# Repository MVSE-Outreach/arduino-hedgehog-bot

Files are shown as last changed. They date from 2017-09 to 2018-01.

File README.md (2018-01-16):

# [Hedgehog Bot](http://hedgehogbot.digimakers.co.uk)

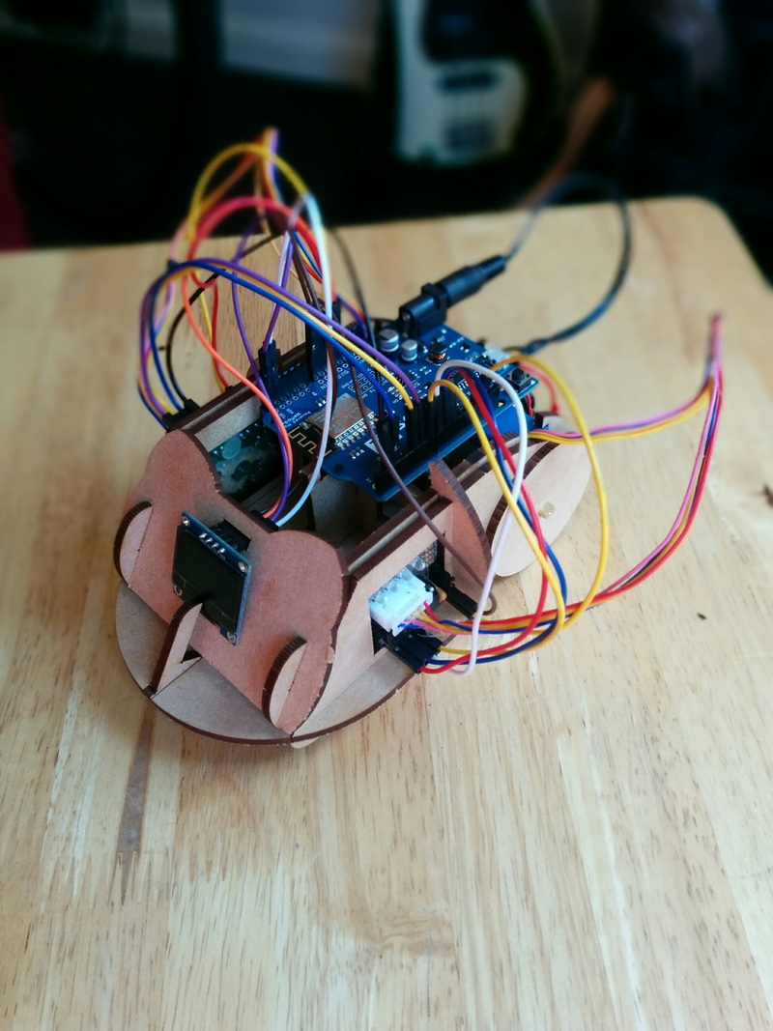
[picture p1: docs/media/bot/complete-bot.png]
Hedgehog bot (http://hedgehogbot.digimakers.co.uk)


The Hedgehog bot is a robotic platform powered by the
[ESP8266](http://espressif.com/en/products/hardware/esp8266ex/overview)-based
[Wemos D1 R2](https://wiki.wemos.cc/products:d1:d1) development board.

Notable Features:
* Full laser cut MDF construction
* Dual servo motor drive
* 128x64 OLED display
* WiFi (client and access point modes)

Instructional videos are available on [YouTube](https://www.youtube.com/playlist?list=PLFSZW1PcP6gNI3f4X1cLMgz0ljdSJu5kU)

If you're interested in learning more, visit the hedgehog bot website:
http://hedgehogbot.digimakers.co.uk 

If you're a volunteer or workshop lead who wants to learn more, check out the
[facilitator notes](#facilitator-notes)

----

## Software setup

### Prerequisites

* [CH340 Drivers](http://www.nerdkits.com/usb-serial/ch341.php)

### Installation
#### Windows or Mac OS X
1. Copy `hhb_blink`, `hhb_bot`, and `hhb_wifi` from `sketches` into your Arduino sketchbook folder
2. Copy the folders in `libraries` to the `libraries` folder in your Arduino
   sketchbook folder, if it doesn't already exist you can just copy and paste
   the `libraries` folder straight into the sketchbook folder.
3. Verify that when you run the Arduino IDE and click the menu options `File -> Sketchbook`
   you can now see:
   - `hhb_blink`
   - `hhb_bot`
   - `hhb_wifi`

#### Linux (Raspberry Pi)

```sh
$ git clone --recursive https://github.com/MVSE-Outreach/arduino-hedgehog-bot.git hedgehog-bot
$ cd hedgehog-bot
$ ./install.sh <PATH-TO-ARDUINO-SKETCHBOOK>
```

----

## Facilitator notes

Most things are documents within the `docs` folder in the repository including:

* Instructions on ordering parts: [docs/kit-ordering.md](docs/kit-ordering.md)
* Troubleshooting: [docs/troubleshooting.md](docs/troubleshooting.md)
* Preparing a workshop: [docs/preparing-a-workshop.md](docs/preparing-a-workshop.md)
* Components used in the Hedgehog bot: [docs/components.md](docs/components.md)

### Laptop setup

* Download the laptop setup script.
* Copy the script over to a memory stick.
* Run the script to set up a computer **at least once** to download the
  necessary dependencies.
* Copy the script along with the files and folders adjacent to the script that
  it downloaded in the previous step to other memory sticks used to set up
  laptops.
* Run the script from the memory stick on all other laptops that need setting
  up, after the first run the dependencies will be downloaded so subsequent
  setups should be much faster.

----

## Known issues
- Arduino Nano not recognised: Have you installed CH340 drivers?
- WiFi not working: Test 9V battery

See the [troubleshooting docs](/docs/troubleshooting.md) for more

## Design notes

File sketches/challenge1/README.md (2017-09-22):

# arduino-sketch-hedgehog-bot-blink

An Arduino Sketch for the HedgeHog bot that blinks the LED on and off.

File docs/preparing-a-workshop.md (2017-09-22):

# Preparing a workshop

## Ordering parts

### Suppliers

[Aliexpress](https://www.aliexpress.com/) has the best prices for the parts we
use, however it has lead times of ~40 days so is best suited to bulk orders
for 100s of kits.

[Banggood](https://www.banggood.com/) has traditionally been the source of
parts for the kits with slightly better shipping times than Aliexpress,
typically 7-20 business days.

[eBay](http://ebay.co.uk/) and [Amazon](amazon.co.uk) have been used for parts
when we've been up against short deadlines needing to prep for workshops with
a few weeks notice. It tends to cost a lot per bot, hence whenever we can we
try and buy from China.

Banggood is considerably more expensive than Aliexpress (Will Price conducted
a comparison in Sept 2017 for pricing for 100 bots, Aliexpress came out at
~£10/bot, and Banggood at ~£18/bot).

Both [buyabattery.co.uk](https://www.buyabattery.co.uk/procell-9v-batteries-box-of-50-bulk-now-duracell-industrial.html),

[batterystation.co.uk](https://www.batterystation.co.uk/9v-batteries/industrial-by-duracell-9v-pp3-6lr1-id1604-batteries-box-of-50),
and [LYCO](https://www.lyco.co.uk/duracell-industrial-alkaline-batteries-9v-pack-of-50.html)
provide good prices for 9V batteries in boxes of 50 pieces. They Have next day delivery for not much money.

### Choosing a supplier

Factors of consideration:

* How long have you got until the workshop?
* How many kits do you need?
* How many kits are in currently in inventory?
* How long until you need the parts in working days? Remember it takes a full
  day to put together a set of kits and you'll need to organise people to help
  you do this. It takes a while for the order to filter through university
  purchasing and actually be placed, again you have to account for this.

| Supplier | Typical lead time (working days) | Comments |
|---|---|---|
| [Aliexpress](https://www.aliexpress.com/) | 40 | We haven't had experience placing an order from Aliexpress yet |
| [Banggood](https://www.banggood.com/) | 7-20 | Typically arrive in under a month from placing an order |

## Putting together kits

* Choose an afternoon and advertise for helpers on the SCEEM facebook group (3 or
  4 is a good number)
* Get envelopes to store each kit in
* Set up a packing line to produce kits
  * Each person is responsible for placing a small number of components into
    the envelope they are passed. They should have the parts close to them to
    minimize the time it takes to put parts into the kits.
  * Check the first kit produced by the packing line against the kit listing
    to ensure no parts have been missed

## Setting up university laptops

NOTE: You'll need admin access to set up a university laptop.

Follow the [installation instrutions](laptop-setup.md).

## Sampling and verifying kits (with university laptops)

* Randomly sample 10% of the kits you have prepared
* Check all parts are present
* Build the kits following the instructions on [hedgehogbot.co.uk](http://hedgehogbot.co.uk)
* Program each of the bots with
  [challenge2](http://www.hedgehogbot.co.uk/challenge2.html) ensuring that the bots can move and the screen displays a face

## Final checks

* [ ] Ensure all the laptops that are going to the workshop have been set up.
* [ ] Ensure you have enough kits for the workshop (ideally bring 10% extra).
* [ ] Plan for component failure and bring spares of each component.
* [ ] Bring files in case the bodies are incorrectly produced and need fettling.

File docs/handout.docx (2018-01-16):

# Hedgehog bot

# Parts checkt

Check that you have the following parts in your pack.

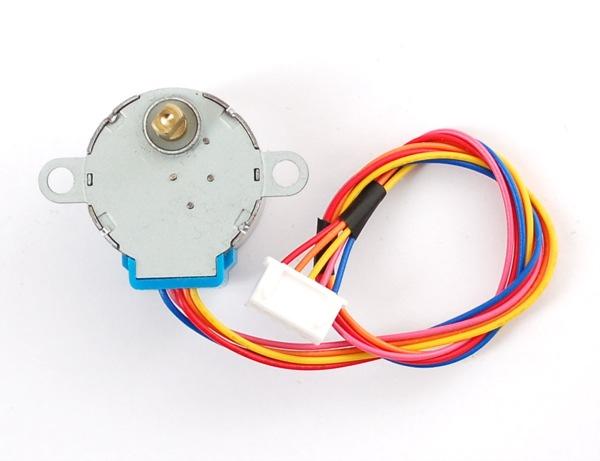
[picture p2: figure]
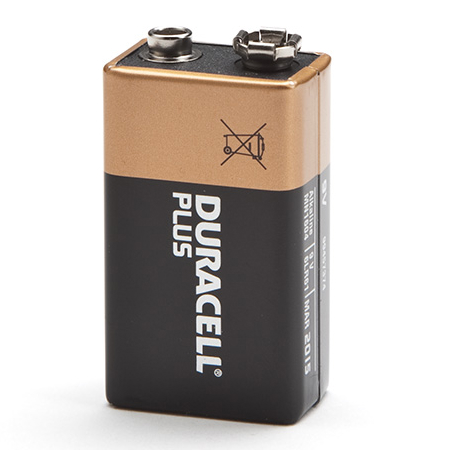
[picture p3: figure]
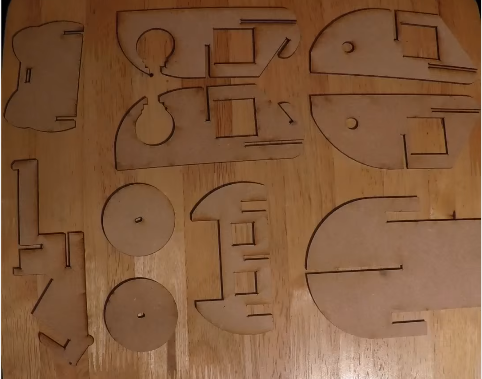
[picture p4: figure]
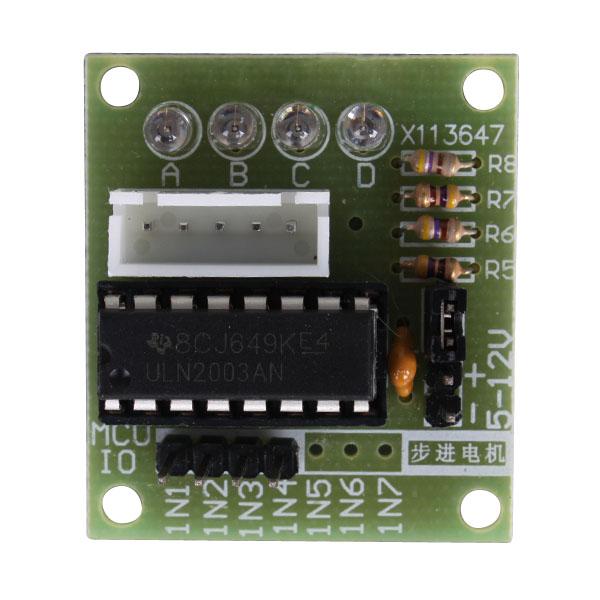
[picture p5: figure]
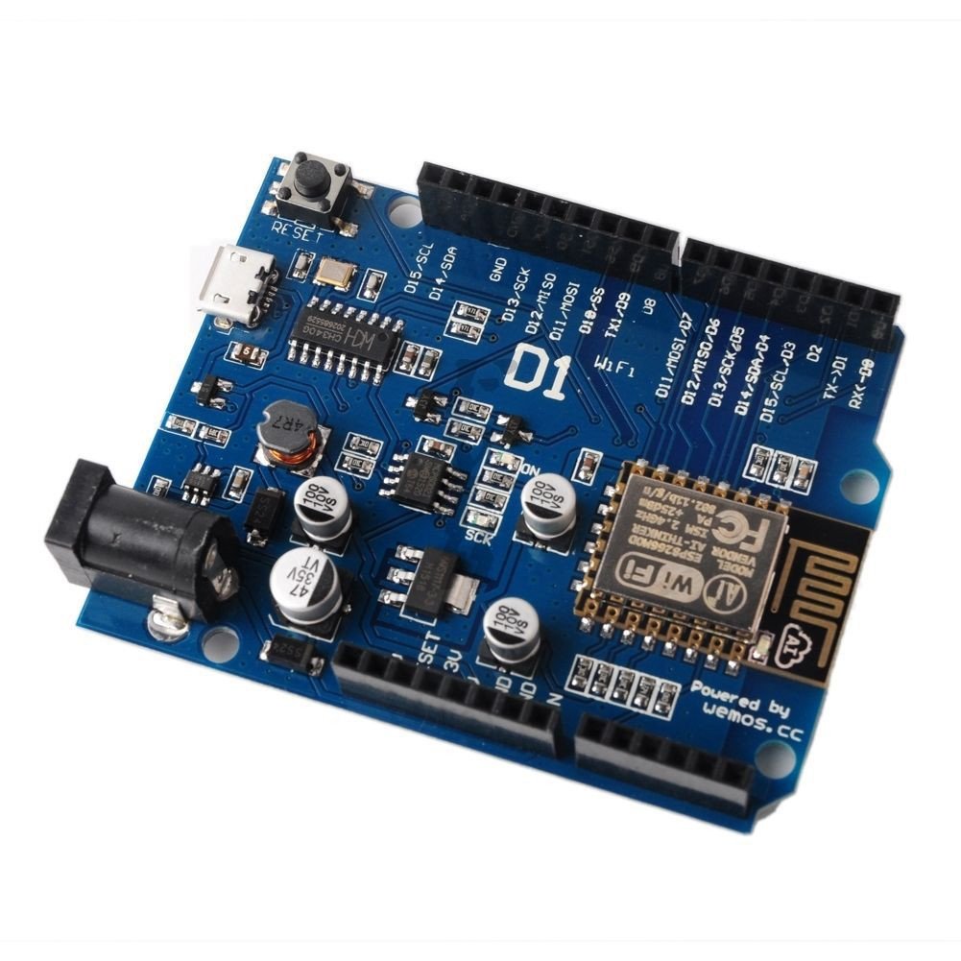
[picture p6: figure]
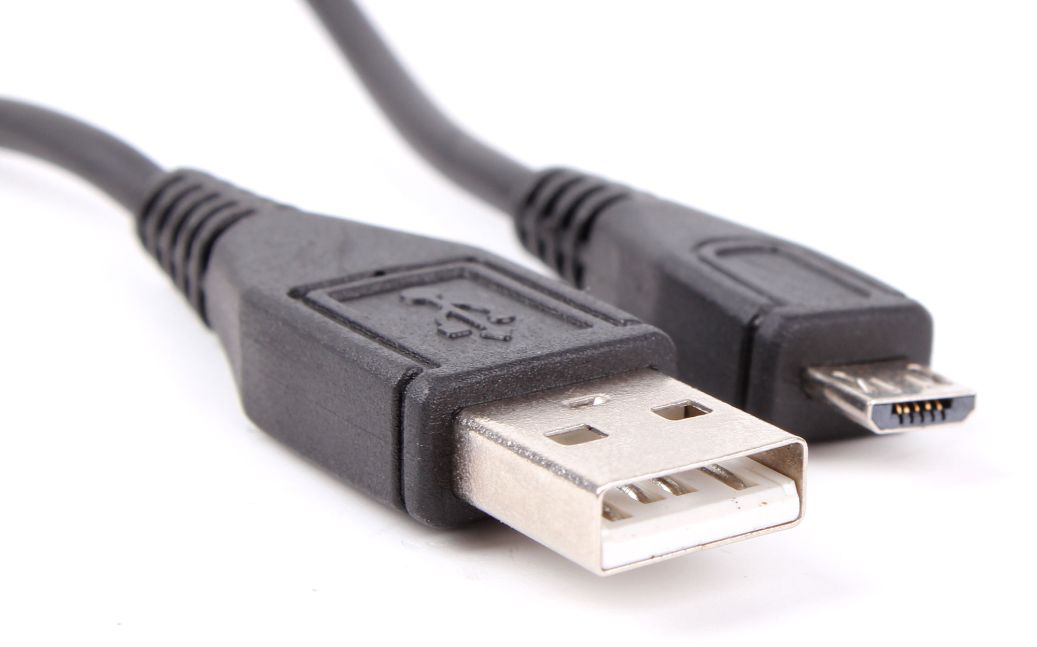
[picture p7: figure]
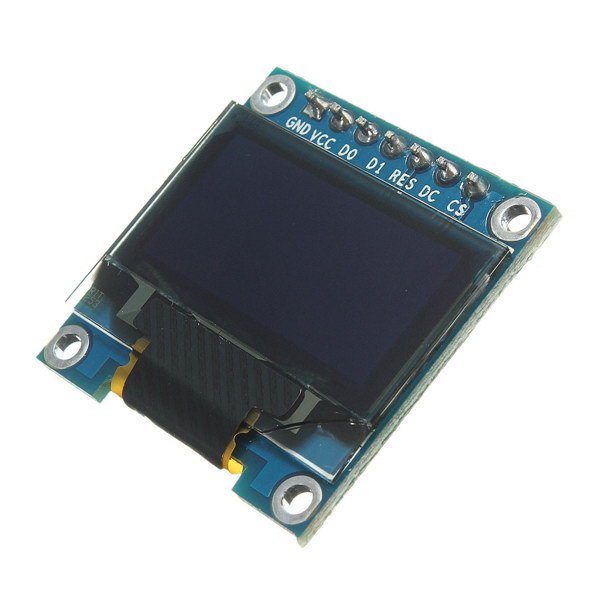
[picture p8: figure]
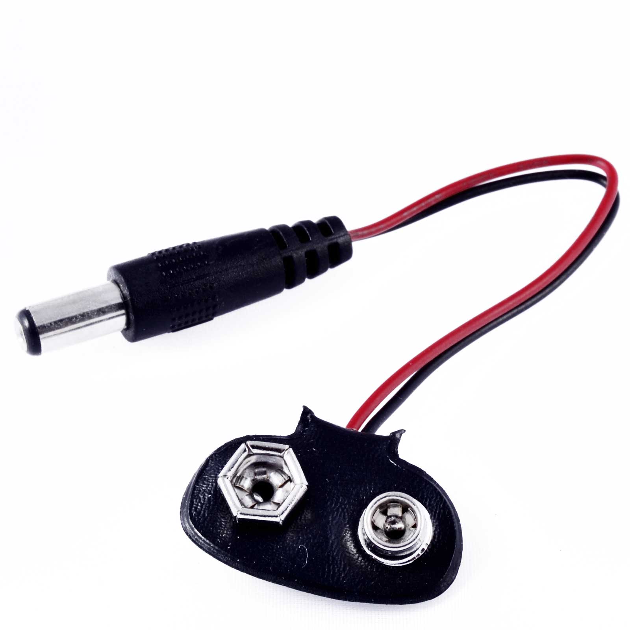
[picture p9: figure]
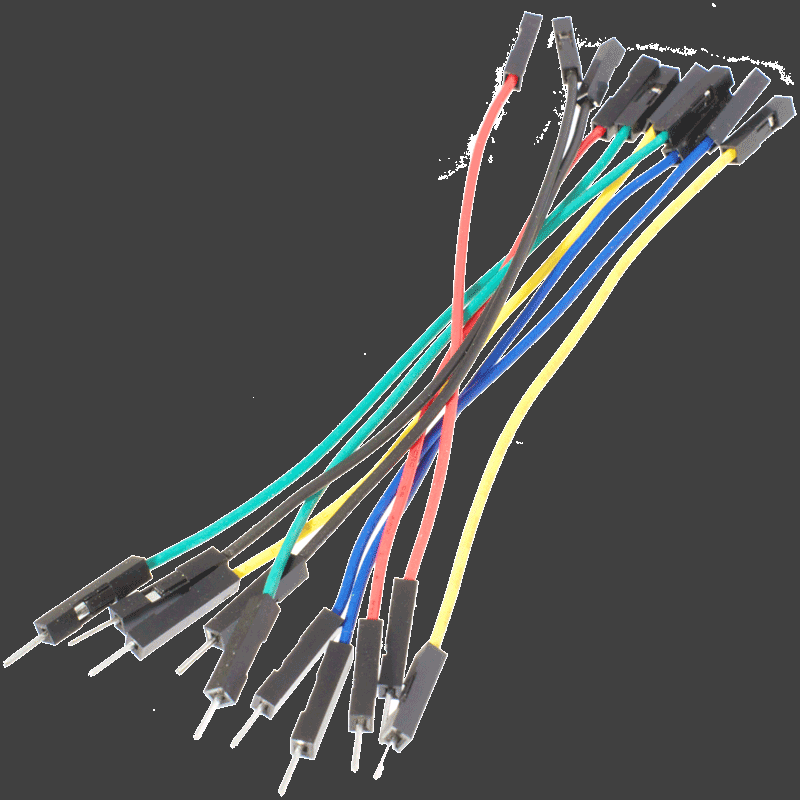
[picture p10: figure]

# Computer setup

Open http://www.hedgehogbot.co.uk/setup.html to setup your computer with the Arduino IDE, esp8266 board package for Arduino, and the hedgehog bot libraries.

In short:

- Grab a memory stick
- Copy and paste the Arduino setup file and extract/run it
- Open Arduino, select File > Preferences and type http://arduino.esp8266.com/stable/package_esp8266com_index.json into Additional Boards Manager URLs
- Close the Preferences window
- Select Tools > Boards > Board Manager and click on esp8266 and press the Install button
- Close the Board manager window
- Copy the contents of the folder Arduino > All > libraries to Documents > Arduino > Libraries

# Get building!

Open http://www.hedgehogbot.co.uk/ and select “Challenge 1: LED”, or if you’re still waiting to setup your computer, skip ahead and start building your robot by looking at “Challenge 2: Bot”, you can go back to Challenge 1 once your bot is built.

Progress through challenges 1-3.

We’re here to help, if you get stuck, please come and ask one of us for help. If you’ve completed all the challenges and want to go further, come and have a chat too!

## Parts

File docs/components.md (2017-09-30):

# MDF body

* 3mm MDF
* If producing cuts for other pieces to fit into, take account of total width of pieces 
  and add ~0.3mm extra for a bit of room otherwise the bits are very hard to put together

# ULN2003 driver boards

* ULN2003 driver
* 32x35x1.5mm
* 4 pin input: IN{1..4}
* 4 pin power input: Vdd, Vcc, jumper to determine whether board is on or off (jumpered = on)

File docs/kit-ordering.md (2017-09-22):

# Ordering in bulk to produce a kit

## Part list

| Part image | Part | Quantity per bot | Comments |
|---|---|---|---|
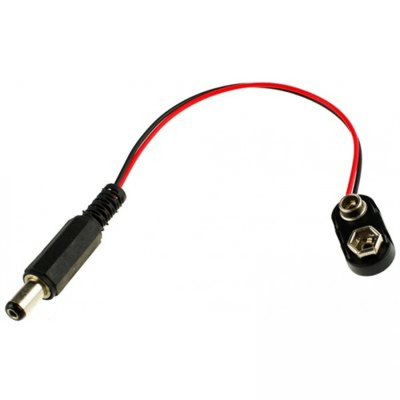
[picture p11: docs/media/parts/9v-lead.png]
9V lead
|  | 9V Lead with barrel jack | 1 | Make sure you get leads with a barrel jack |
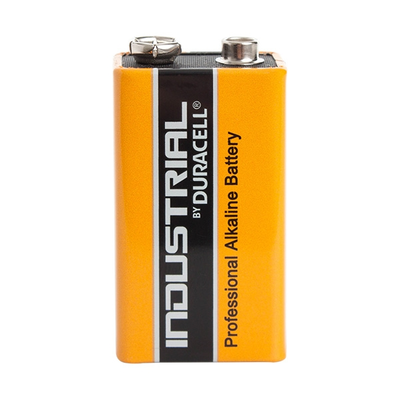
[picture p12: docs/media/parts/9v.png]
9V battery
|  | 9V battery | 1 | Sometimes kids go through more than a single battery in a single session |
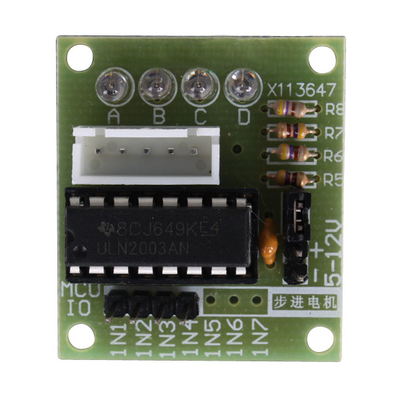
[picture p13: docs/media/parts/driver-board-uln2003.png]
Motor drive board
|  | ULN2003 Stepper motor driver board | 2 | Needs to be this exact board as the body is designed for it |
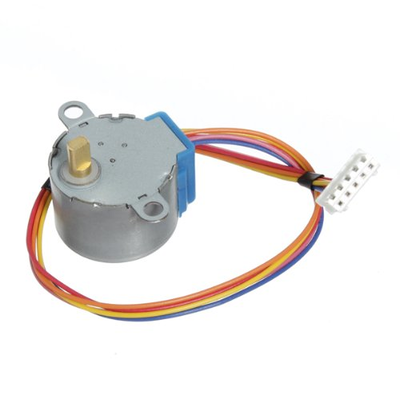
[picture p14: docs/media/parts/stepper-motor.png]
Stepper motor
|  | 28YBJ-48 Stepper motor | 2 | |
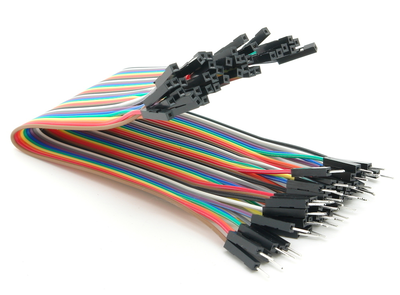
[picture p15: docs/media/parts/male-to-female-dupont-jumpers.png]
Male to female dupont jumpers
|  | Male to female dupont jumper cable | 20 | |
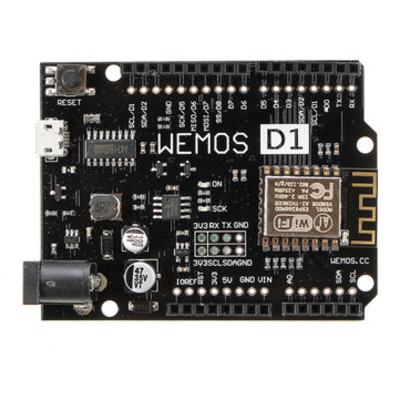
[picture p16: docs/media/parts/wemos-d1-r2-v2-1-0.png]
Wemos D1 R2 v2.1.0
|  | Wemos D1 R2 (v2.1.0) | 1 | |
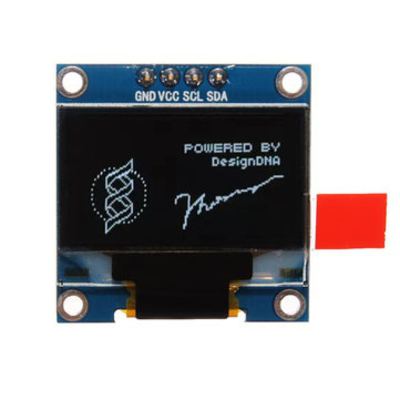
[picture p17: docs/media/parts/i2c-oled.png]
I2C 0.96" OLED
|  | I2C 128x64 0.96" OLED screen | 1 | 4 pins (GND, VCC, SCL, SDA) |
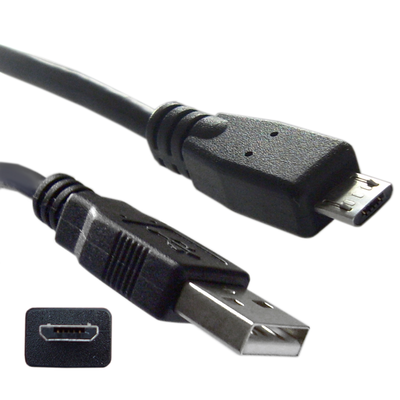
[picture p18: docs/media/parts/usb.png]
USB cable
|  | Micro USB cable | 1 | Observed about a 5% failure rate in the cheap one we buy |

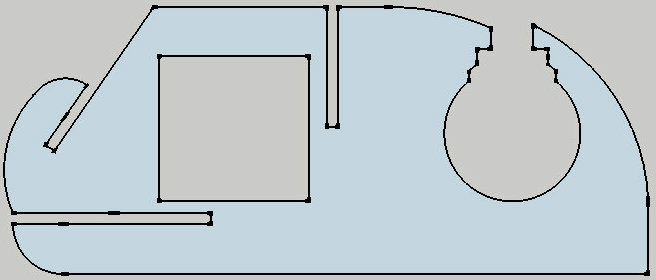
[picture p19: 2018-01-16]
docs/media/body-parts/inner side.jpg

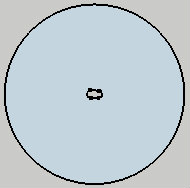
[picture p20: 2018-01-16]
docs/media/body-parts/wheel.jpg

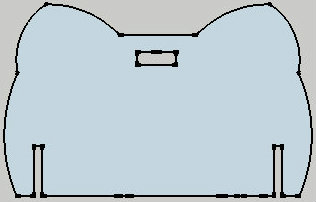
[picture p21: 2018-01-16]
docs/media/body-parts/face.jpg

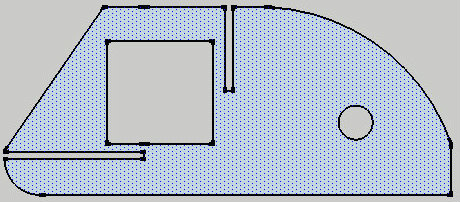
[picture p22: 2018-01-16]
docs/media/body-parts/outer side.jpg

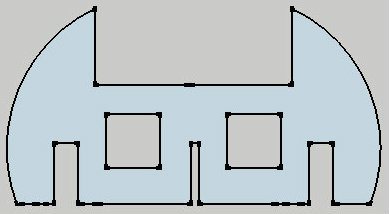
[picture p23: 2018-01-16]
docs/media/body-parts/middle.jpg

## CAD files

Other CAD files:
body/v2/bodyV2_5_255mm_285mm.dxf
body/v1/bodyv2_255mm_285mm_release.dwg
body/v1/OLED+LCD+0_96+.skp
body/v1/ULN2003-0.skp
body/v1/arduinoleonardo.skp
body/v1/battery+9V.skp
body/v1/body scott jerk face.skp
body/v1/bodyV2 rough scott.skp
body/v1/body_joe.skp
body/v1/bodyv2_255mm_284mm_release.skp
body/v1/stepper.skp
body/v2/bodyV2_5_255mm_285mm.dwg

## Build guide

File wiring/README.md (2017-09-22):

# Wiring Diagrams

The wiring diagrams in the directories below have been produced with
[fritzing](http://fritzing.org/home/).

Install Fritzing, and open any of the wiring diagrams (files ending in `.fzz`).

If you want to create new wiring diagrams you might want to add the
parts to your Fritzing library. To do so, open up Fritzing and in the
*Parts* widget, click the top right drop down menu and select *Import*
and open an *.fzpz* file which will be imported into the *Mine* parts
bin.

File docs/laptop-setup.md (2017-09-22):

# Laptop setup for the Hedgehog Bot workshop

These instructions will show you how to set up a laptop ready to be used for
the hedgehog bot workshop.

* [ ] Install the [Arduino IDE](https://www.arduino.cc/en/main/software)
* [ ] Install the [ESP8266 Arduino core](https://github.com/esp8266/Arduino)
  * Open the Arduino IDE
  * Navigate to *File > Preferences* (`<Ctrl-,>` to quickly launch it)
  * Paste `http://arduino.esp8266.com/stable/package_esp8266com_index.json`
    into the *Additional Board Manager URLs* field.
  * Open *Tools > Board > Boards Manager*, search for `esp8266`, select the latest version and click *Install*
* [ ] Verify Wemos connectivity
  * Open the Arduino IDE
  * Check for any listings under *Tools > Port*, take note of them
  * Plug in a Wemos
  * There should now be an additional listing under *Tools > Port* representing the Wemos
  * If there isn't a listing, then install the [CH340
    Drivers](http://www.nerdkits.com/usb-serial/ch341.php) and try again, it
    should show up after a driver install.
* [ ] Verify programming support
  * Open the Arduino IDE
  * Open *File > Examples > ESP8266 > Blink*
  * Click the upload button (right of the tick button)
  * Verify that the wemos LED has started blinking and the program has successfully uploaded

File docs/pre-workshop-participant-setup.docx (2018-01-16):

Hello participants,

I ask that you could follow some preparatory steps to ready yourself for the Hedgehog workshop on Saturday. If you have any issues following these instructions, don't worry, we'll help you get set up on Saturday.

We need the Arduino software setup with esp8266 drivers, follow the instructions on the hedgehog bot website

(http://www.hedgehogbot.co.uk/setup.html)In brief, the instructions from the above website link are:

1. Download and install the Arduino software
2. (https://www.arduino.cc/en/Main/Software)Open Arduino, select File > Preferences and type http://arduino.esp8266.com/stable/package_esp8266com_index.json into Additional Boards Manager URLs
3. Close the preference window
4. Select Tools > Boards > Board Manager and click on esp8266 and press the Install button
1. Download the library ZIP file
2. (https://drive.google.com/open?id=0B-sOGxoTtrCcWnNKak55WnVPYlU)Right click the file, and select extract all
3. Select all the extracted folders and copy them into My Documents\Arduino\libraries

Having problems, need help? On Saturday, ask the front desk for the help desk who will help you setup your laptop for the workshop.

We’re looking forward to seeing you all there and building robots!

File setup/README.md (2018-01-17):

# Installation scripts

The primary script is targeted at Windows, as most of our users are on that
platform.

## Windows set up

Copy the `windows-setup.ps1` script to a memory stick and run it on a computer
you wish to set up. It will cache the dependencies alongside the script so that
subsequent runs will be faster as nothing will have to be downloaded.

## Linux set up

Run `linux-setup.sh` to install sketches and libraries to arduino folder.

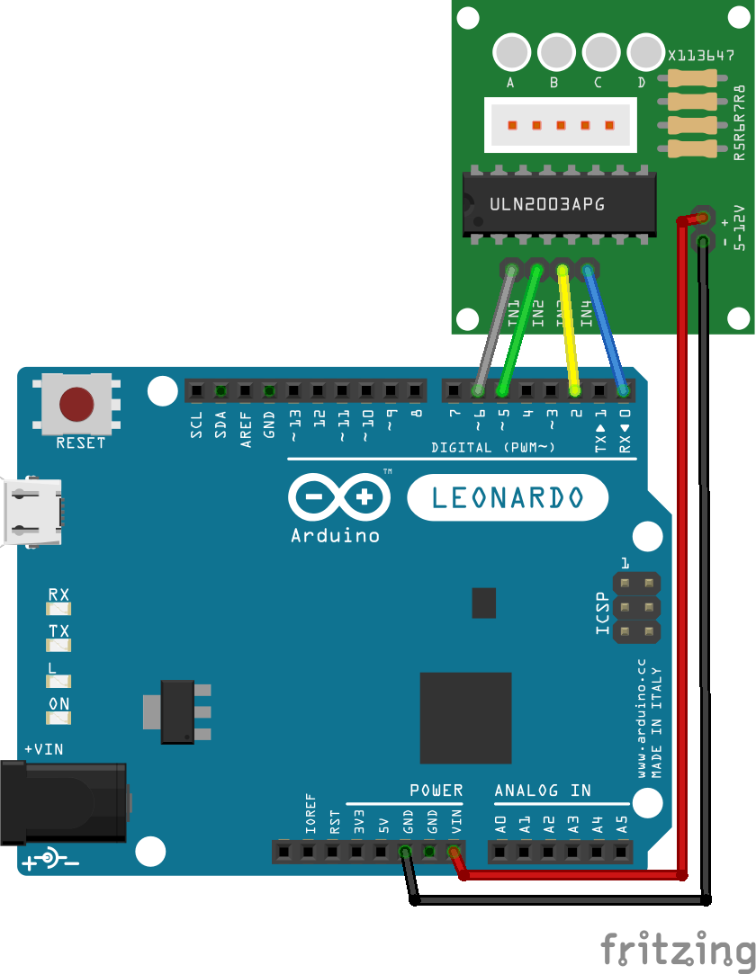
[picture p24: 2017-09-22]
wiring/v2/media/rightmotor_bb.png

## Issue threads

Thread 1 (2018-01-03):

CH340 Drivers

jda0, 2018-01-03:
- Add support for Mac following steps at [https://arduino.stackexchange.com/a/17358]()
- Include copies of CH340 drivers for Win/Mac in repo for safekeeping?

willprice, 2018-01-15:
The Wemos wiki actually has a link for the drivers: https://wiki.wemos.cc/products:d1:d1 we should probably link there.

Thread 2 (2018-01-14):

Determine which board versions work with the current instructions

willprice, 2018-01-14:

willprice, 2018-01-14:
**Versions**:
* OS: Windows 10 (x64)
* Arduino version: 1.8.5
* esp8266-boards version: 2.4.0

**Arduino board settings:**
* Board: WeMos D1 R2 & Mini
* Flash size: 4M (1M SPIFFS)
* Debug port: Disabled
* Debug level: None
* IwIP Variant: v2 Prebuilt (MSS=536)
* CPU Frequency: 80MHz
* Upload Speed: 921600

| Board | Works? | Notes |
|--------|----------|--------|
| Wemos D1 R2 v2.1.0 (Black) - Wemos marked | Yes | |
| Wemos D1 R2 (Blue) - Wemos marked | Yes | |
| Wemos D1 (Blue) - not Wemos marked | Nope | Wiring up visually does not work, had to rewire SDA/SCL of OLED, its impossible to wire up according to pinout. |

For the D1 R1 we can rewire the SDA/SCL pins easily, the motor pins need completely remapping

Other notes:

* I had updated the libraries through the library manager but this messed up `ESP_SSD1306`  library.
* The pin `RX` is not found -> using wrong board config (D1 R1 - should be D1 R2 & mini)

willprice, 2018-01-15:
I'm testing a bunch of boards with `blink` to see how the LEDs are wired up.

**Arduino board settings:**

* Board: WeMos D1 R2 & Mini
* Flash size: 4M (1M SPIFFS)
* Debug port: Disabled
* Debug level: None
* IwIP Variant: v2 Prebuilt (MSS=536)
* CPU Frequency: 80MHz
* Upload Speed: 921600

| Board | On board LED test (active high or low?) | IO LED test (active high or low?) (LED pin = D0) |
| Wemos D1 R2 v2.1.0 (Black) - Wemos marked | Active low | D0 didn't work |
| Wemos D1 R2 (Blue) - Wemos marked | Active low | Active high |
| Wemos D1 (Blue) - not Wemos marked | Active low | Active high |

It seems the builtin LED is active-low for all board revisions.

I had issues with a v2.1.0 not uploading on Windows 10, swapped on the USB cable, no change, swapped out the board started working, swapped board back in started working... put on desk, tried again, stopped working, held up in air and programming succeeded, wiggled usb cable up and down (force on the connector) and programming succeeded, tried again and it failed, next time succeeded, next time succeeded, next time succeeded. Seems this is not the first time people have experienced the issue:

* https://github.com/esp8266/Arduino/issues/2604g

Tried 6 v2.1.0 to replicate failing upload but all succeeded, even when rubbed on my fleece to add some static to the system.

willprice, 2018-01-15:
https://github.com/esp8266/Arduino/issues/3760 notes that flashing at 921600 "is just asking for trouble", so perhaps we should put the upload speed to a lower default

willprice, 2018-01-15:
[Schematic](https://wiki.wemos.cc/products:d1:d1_mini) shows that the Wemos D1 mini has an active low status LED (`GPIO14`), and since the D1 R2 has the same chip stuck to the board we can conclude this is design.

(noted in https://github.com/esp8266/Arduino/issues/1780)

willprice, 2018-01-16:
Closed in favour of #4 as the write up above details the behaviour of the v2.1.0 boards vs the older blue boards (and the really old D1 R1 boards)

Closed 2018-01-16.

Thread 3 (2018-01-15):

Website: fix hedgehogbot.co.uk links

willprice, 2018-01-15:
The challenge page buttons at the bottom for going forward or backward a challenge are broken, the links need updating.

Closed 2018-01-16.

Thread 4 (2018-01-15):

Website: correct challenge 1

willprice, 2018-01-15:
The builtin LED is active low not active high, so the example sketch and accompanying text need changing to correct this + explain what active low/high is.

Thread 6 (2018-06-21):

Rewrite HTML in Markdown to ease development

jda0, 2018-06-21:
**STATUS: Underway**
Online preview at [jamesin.space/hedgehog/challenges/1-led](https://jamesin.space/hedgehog/challenges/1-led)

New template creates:
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

From:
```markdown
---
title: LED
description: This is the first challenge - learn some programming and create some Morse code!

requires_kit: board-only
language: Arduino C
est_time: 10&mdash;20min
difficulty: Easy
completion:
  - LEDs
  - Loops
  - Delays
  - Morse code

header_img: /assets/media/hedgehog-led-top.svg
header_bg: "#FAF5FF"
---

1.  #### Setup your computer
    1. Download Arduino IDE from [arduino.cc](https://www.arduino.cc/en/Main/Software),
        install and open it.
    2. Click **File&rarr;Preferences**, and paste
        `http://arduino.esp8266.com/stable/package_esp8266com_index.json` into
        **Additional Boards Manager URLs**.
    3. Click **Tools&rarr;Board&rarr;Boards Manager...**,
        then click **Type&rarr;Contributed** followed by
        **esp8266 by ESP8266 Community**. Click **Install**.

2.  #### Connect the board
    1. Connect the WeMos board to your PC using the microUSB cable.
    2. Click **Tools&rarr;Board&rarr;Wemos D1 R2 & Mini**.
    2. Click **Tools&rarr;Port&rarr;COM*x***, where ***x*** is any number
        greater than 1.

3.  #### LEDs and Loops
    A LED (Light Emitting Diode) is a little light which is built into your
    WeMos. It's a great thing to use to try out some code. Before you start
    coding, you need to know about comments, the setup and loop:
    ```c
    // this is a comment, started with a //
    // it is used to explain something in your code

    void setup() {
      // here, between the {} we're inside the setup
      // this happens first to set up things!
    }

    void loop() {
      // here, between the {} we're inside the loop
      // this happens after the setup
      // this then repeats over and over again forever!
    }
    ```

4.  #### Blink Code
    The builtin LED is an Active LOW component meaning that setting it LOW
    turns it on and setting it HIGH turns it off. Active HIGH components turn
    on when set HIGH and turn off when set LOW.

    Have a look at the code below. This code will:
    1. turn off the LED for one second
    2. turn on the LED for one second
    3. repeat over and over!

    ```c
    void setup() {
      pinMode(BUILTIN_LED, OUTPUT); // set up the LED
    }

    void loop() {
      digitalWrite(BUILTIN_LED, HIGH); // turn off LED
      delay(1000); // wait one second
      digitalWrite(BUILTIN_LED, LOW); // turn on LED
      delay(1000); // wait one second
    }
    ```
    {: .ide}

    1. Copy the code above and paste into the Arduino IDE
    2. Press the upload button <i class="arduino-upload"></i>. You'll see the
        code compiling and uploading in the black box at the bottom. When it's
        done you should see '*Done Uploading*' just above the black box.
    3. You should see an LED flashing on and off once a second on the WeMos!
    4. Now try changing the size of the delays - what do you think will happen
        if the delays are 2000 milliseconds instead of 1000? Upload the code to
        see!

5.  #### Morse Code
    Now you know how to change the speed of flashing of your LED, let's use that
    to make some Morse code! Your challenge is to spell **SOS** using the LED.

    Use the chart below for help. A dot is a short pulse of light, and a dash is
    a long pulse. Don't forget to add an extra delay at the end of the word.

    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
```

jda0, 2018-06-21:
Online preview at [https://jamesin.space/hedgehog/challenges/1-led]()

jda0, 2018-06-21:
All pages have now been transferred to the new format:
- jda0/hedgehog@ee6563b
- [jamesin.space/hedgehog](https://jamesin.space/hedgehog)

jda0, 2018-06-21:
Commit history has been merged into the working repo (to facilitate merge back). This remote is referred to as `live`.
- jda0/hedgehog@082ec00

Just requires adding `CNAME`: `echo "hedgehogbot.digimakers.co.uk" > CNAME && git commit -am "Add CNAME" && git push live gh-pages`

jda0, 2018-06-22:
Added CNAME, pushed to fork jda0/arduino-hedgehog-bot@9f7f2d9 and created PR #7

Closed 2018-07-23.

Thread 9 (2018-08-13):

Revise workshop durations

jda0, 2018-08-13:
Currently, the workshop times are given as:
 - LED, Bot, Wifi: 10-20mins Easy
 - Clock: 30-60mins Intermediate

As these are definitely too short and may be disphoric, your thoughts/revisions are welcome to changing them to:
 - LED: 15-45mins Beginner
 - Bot, Wifi: 30-60mins Intermediate
 - Clock: 45-90mins Tricky

@willprice (need to get joe's :octocat: )

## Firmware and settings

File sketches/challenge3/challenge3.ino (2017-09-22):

// this code gives your Hedgehog Bot wifi connectivity!

// this stuff helps the arduino understand the wifi chip:
#include "dualStepper.h"
#include "U8glib.h"
#include "drawFace.h"
#include "SoftwareSerial.h"
U8GLIB_SH1106_128X64 u8g1(U8G_I2C_OPT_NONE);
char inChar, inData[6] = {0, 0, 0, 0, 0, '\0'},
             buttonData[7] = {0, 0, 0, 0, 0, 0, '\0'};
int charIndex = 0, buttonPress = -1;
boolean copyChar = false;
SoftwareSerial ESP8266Serial(A0,
                             A1); // call to SoftwareESP8266Serial(rxPin, txPin)

// this tells the arduino how the motors are wired up:
int left1 = 9, left2 = 8, left3 = 7, left4 = 6, right1 = 5, right2 = 4,
    right3 = 3, right4 = 2;

// This tells Hedgehog Bot your wifi info
#define auth "e3c48d32244648998f908a5e9ecac514" // Blynk Auth Token
#define SSID "BT Wifi" // Your Wifi ID
#define PASS "password" // Your Wifi password
String cmd = "###>";

// this is the setup function:
void setup() {
  motor.Enable(right1, right2, right3, right4, left1, left2, left3, left4);
  motor.Stop();
  // Serial.begin(1200); //for debugging purposes
  ESP8266Serial.begin(1200);
  WifiConnect();
  ESP8266Serial.flush();
}

// this loop runs over and over again forever:
void loop() {
  blynkButtons();
  if (buttonPress == 0) {
    motor.Forward();
  }
  delay(100);
}

void blynkButtons() {
  charIndex = 0;
  buttonData[9] = 0, 0, 0, 0, 0, 0, 0, 0, 0;

  while (ESP8266Serial.available()) {
    inChar = (char)ESP8266Serial.read();
    if (copyChar == true) {
      buttonData[charIndex] = inChar;
      charIndex++;
      if (inChar == '\r') {
        copyChar = false;
        break;
      }
    }
    if (inChar == 'V') {
      buttonData[0] = inChar;
      charIndex++;
      copyChar = true;
    }
  }
  ESP8266Serial.flush();
  // Serial.println(buttonData);
  if ((buttonData[0] == 'V') && (buttonData[1] == '0') &&
      (buttonData[4] == '1')) {
    buttonPress = 0;
  } else if ((buttonData[0] == 'V') && (buttonData[1] == '1') &&
             (buttonData[4] == '1')) {
    buttonPress = 1;
  } else if ((buttonData[0] == 'V') && (buttonData[1] == '2') &&
             (buttonData[4] == '1')) {
    buttonPress = 2;
  } else if ((buttonData[0] == 'V') && (buttonData[1] == '3') &&
             (buttonData[4] == '1')) {
    buttonPress = 3;
  } else if ((buttonData[0] == 'V') && (buttonData[1] == '4') &&
             (buttonData[4] == '1')) {
    buttonPress = 4;
  } else if ((buttonData[0] == 'V') && (buttonData[1] == '5') &&
             (buttonData[4] == '1')) {
    buttonPress = 5;
  } else if ((buttonData[0] == 'V') && (buttonData[1] == '6') &&
             (buttonData[4] == '1')) {
    buttonPress = 6;
  } else if (buttonData[4] == '0') {
    motor.Stop();
  }
}

void WifiConnect(void) {
  cmd += auth;
  cmd += ">";
  cmd += SSID;
  cmd += ">";
  cmd += PASS;
  cmd += ">#&\n\r";
  draw.Wifi1();
  delay(10);
  draw.Wifi2();
  delay(10);
  draw.Wifi3();
  while (1) {
    if (ESP8266Serial.find("INITIALISING")) {
      break;
    }
  }
  screenText(0, 16, "connecting to:", SSID, "authentication:", auth);
  delay(1000);

  ESP8266Serial.print(cmd);
  digitalWrite(13, LOW);
  while (1) {
    if (ESP8266Serial.available()) {
      inChar = (char)ESP8266Serial.read();
      inData[0] = inData[1];
      inData[1] = inData[2];
      inData[2] = inData[3];
      inData[3] = inData[4];
      inData[4] = inChar;

      if ((inData[0] == 'R') && (inData[1] == 'e') && (inData[2] == 'a') &&
          (inData[3] == 'd') && (inData[4] == 'y')) {
        screenText(0, 16, "Connection", "established!", "", "");
        break;
      }
    }
  }
  delay(2000);
  draw.Smile();
}

void screenText(int x_pos, int y_pos, char text1[], char text2[], char text3[],
                char text4[]) {
  u8g1.firstPage();
  do {
    u8g1.setFont(u8g_font_unifont);
    u8g1.drawStr(x_pos, y_pos, text1);
    u8g1.drawStr(x_pos, y_pos + 16, text2);
    u8g1.drawStr(x_pos, y_pos + 32, text3);
    u8g1.drawStr(x_pos, y_pos + 48, text4);
  } while (u8g1.nextPage());
}

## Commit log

2017-09-22 Add fritzing wiring diagrams
    [leftmotor.fzz, oledwiring.fzz, rightmotor.fzz]
2017-09-22 [docs] Update drive board picture
2017-09-22 Add body files from google drive
    [OLED+LCD+0_96+.skp, ULN2003-0.skp, arduinoleonardo.skp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]
2017-09-22 Add Fritzing wiring readme
2017-11-23 Add new body revision (v2.1)
    * Has version number of sides
    * Batman piece is now correct
    * The bit that holds the wemos is still ~1mm too narrow
    [bodyV2_5_255mm_285mm.dxf]
2018-01-29 Add HHB body v2.2
    Adjust batman slit width to 7.625mm and batman arduino slot width to 54mm from 52mm as the Wemos D1 R2 v2.1.0 (black) boards seem to be wider than the v2.0.0 (blue) boards
    [bodyV2_5_255mm_285mm.dwg, bodyV2_5_255mm_285mm.dxf]
